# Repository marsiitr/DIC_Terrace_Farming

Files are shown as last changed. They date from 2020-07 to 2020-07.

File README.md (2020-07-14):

# DIC_Terrace_Farming
 Inter IIT Tech Meet 2019

<p align="center">
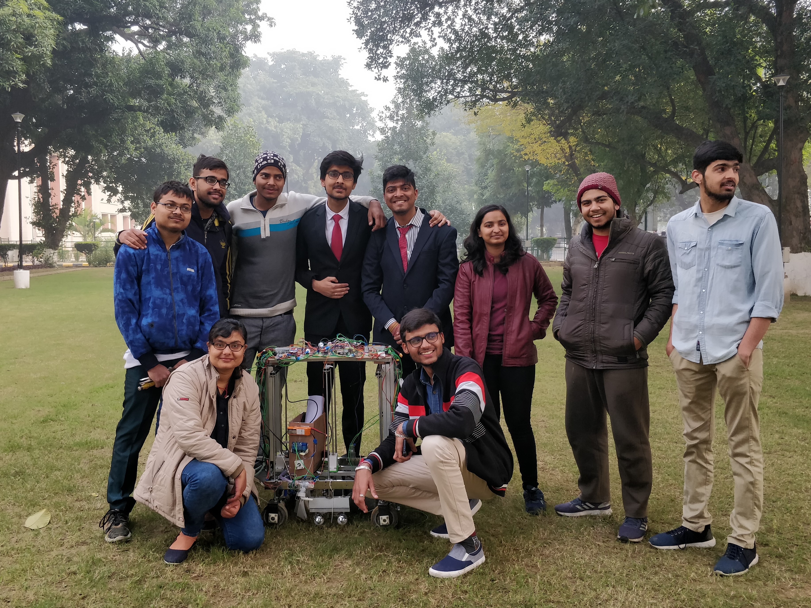
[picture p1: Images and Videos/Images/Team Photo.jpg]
  
  Team MaRS @Inter IIT Technical Meet 8.0
</p>

## Abstract:
<p align="justify">MaRS IIT Roorkee has developed an autonomous bot to perform agricultural tasks for terrace farming. This bot can perform functionalities like seeding, watering, ploughing and harvesting of the crops. It is itself unique in a way that the bot can climb up and down the manmade steps in the terrace farming.</p>

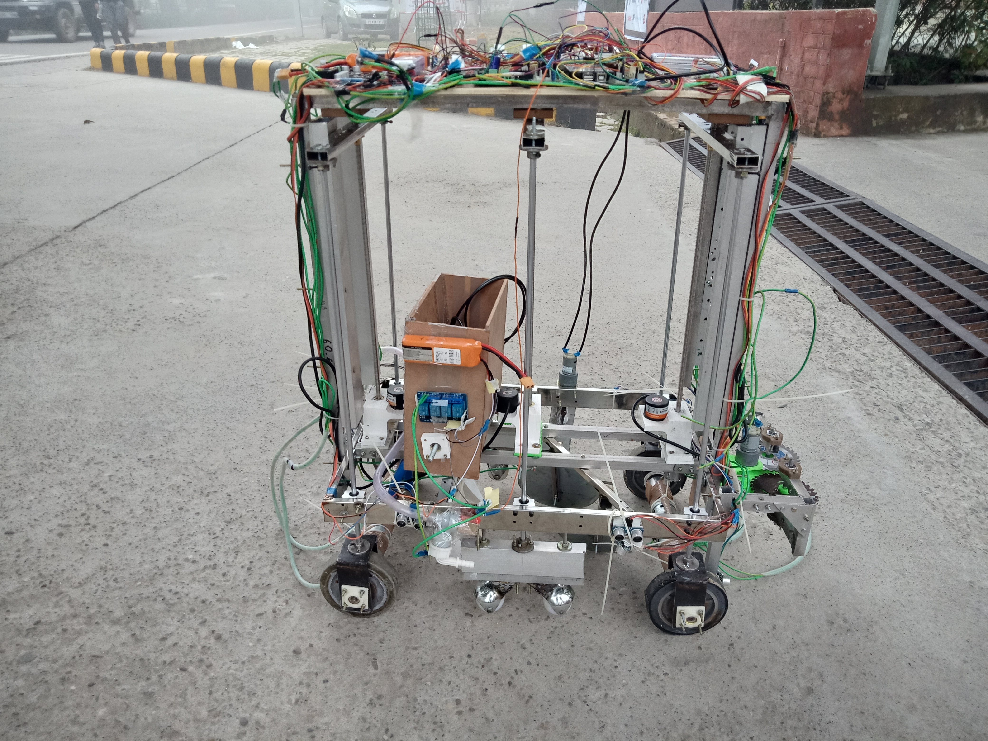
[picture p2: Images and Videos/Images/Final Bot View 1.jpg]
Terrace Farming Robot


To view more images of the final bot, click [here.](https://github.com/visvash/DIC_Terrace_Farming/tree/master/Images%20and%20Videos/Images "DIC_Terrace_Farming_Robot")

### Challenges faced in Terrace Farming:
* Narrow terraces make it difficult for the farmers to navigate. These also prevent the use of heavy machinery or animal power thus the farmers have to rely on locally made agricultural tools which are appropriate to narrow terraces. The use of improper tools and methods lead to poor yields.
* Improper irrigation methods and shortage of watering systems hamper the growth of the crops.
* Wider terraces demand the use of draft animals as a source of farm power. Sometimes farmers are compelled to use manual labour even for ploughing.
* Steeper slopes make it difficult for the farmers to mobilise the farming tools. It drastically increases the labour demand and hence increasing the cost of production.

## Mechanical Aspects of the Design

### Traversal
* The bot uses 4-wheel differential drive to traverse on the soil surface. Two central idler wheels are provided for extra stability while climbing the steps and traversing on uneven surfaces.
* For this drive we are using Mega Torque Planetary DC geared motor of 300RPM and torque capacity of 92kg-cm, enough to carry out tasks like Ploughing and Seeding. The chassis of bot is made up of square steel pipes, arc welded together for rigidity.

### Climbing
* We divided bot into 3-wheel assemblies in which front and back are containing 2 wheels, 2 motors and a lead screw but the middle assembly contains 4 caster wheels and a lead screw so that the bot does not topple, while one of the front or back wheel assemblies is in the air.
* In the first step, the whole body will be lifted by actuating the lead screws of middle and rear wheel assemblies. Then the bot will move forward until the front wheels rest above the step.
* In the second step, the Middle Caster Wheels will be pulled back up and the bot will move forward by actuating the back wheels to rest on the stair on front and middle wheels.
* In the last step, the back wheels will be pulled up, this time the front wheels will be actuating and it will move the bot forward and the bot would have climbed up.
* The bot also has an ability to lift itself above the crop for traversing in the field.

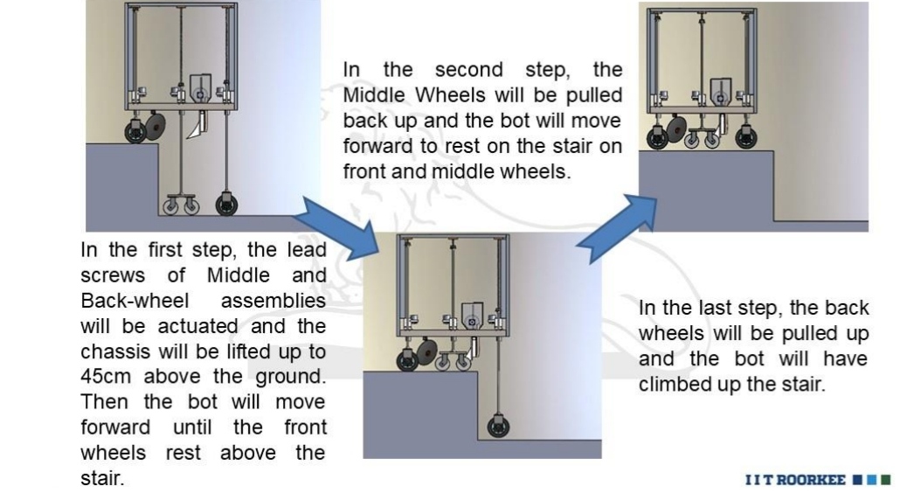
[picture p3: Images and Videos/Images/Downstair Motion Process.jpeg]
Climbing Process


### Ploughing
* The thickness of Topsoil for cultivation in terraces is less in comparison to that of plains and we can encounter stones while deep ploughing.
* Using a Disc Harrow mechanism for shallow ploughing would be more appropriate and will save the Tool from wear and tear. Simultaneously it will use less Power per unit area.
* A special concave disk having an angle of curvature of around 15-25 degrees has been used. This angle determines the ploughing depth. More the angle more is the depth of plough and more is the power to drive the operation.
* The discs also maintain an angle of 40-45 degrees with the direction of travel which helps it in rotation and opening of the soil by scooping it out simultaneously.

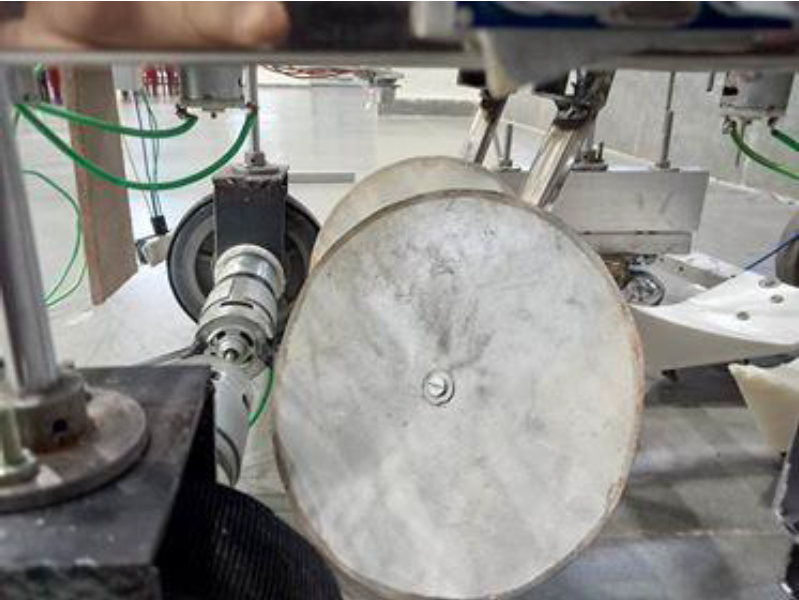
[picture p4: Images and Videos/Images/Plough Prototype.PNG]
Plough


### Watering
* The bot will have a solenoid-valve for electronically controlling the water given to the crops. 
* The concept of the watering mechanism is designed so as to minimize the water consumption along with maintaining the net yield.

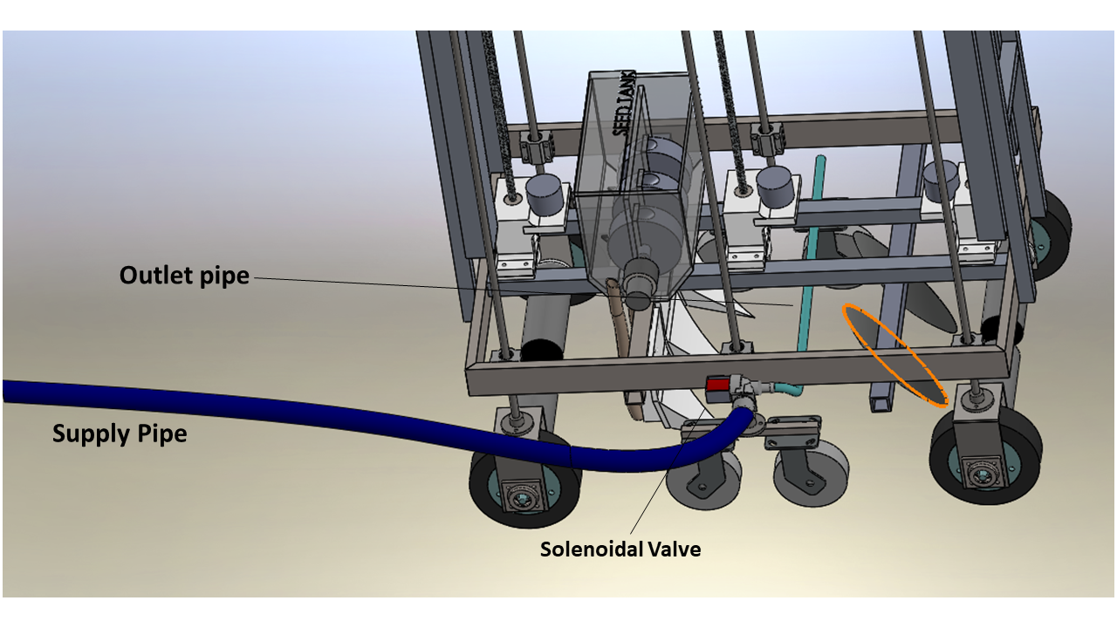
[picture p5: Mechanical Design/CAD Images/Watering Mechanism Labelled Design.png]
Watering Mechanism Design


### Seeding
* For dropping the seeds, a seed tank is attached on the bot that directs the seeds to the outlet pipes using 3D printed discs controlled by Johnson type DC motor. The tank contains 3 circular disc-like structures with grooves in them. These discs are rotated by the motor.
* The tank is divided into two-compartments, one compartment contains the seed and the other compartment contains the outlet. When the motor rotates the disc, the seeds are trapped in the grooves and are transferred to the next compartment. The seeds then fall to the ground through the outlet.
* Cultivator is mounted at the bottom along with outlet pipes at their back so they easily drop off seeds in the tillage so formed.

### Harvesting
• Harvester consists of 2 cutting blade, operated by a geared DC motor using Spur Gears.<br>
• Both the blades will rotate with the same speed but in opposite direction, the blades share a common
cutting area which will ensure cutting of crop which comes in between them.<br>
• The harvester can be detached and can be mounted on bot when required.

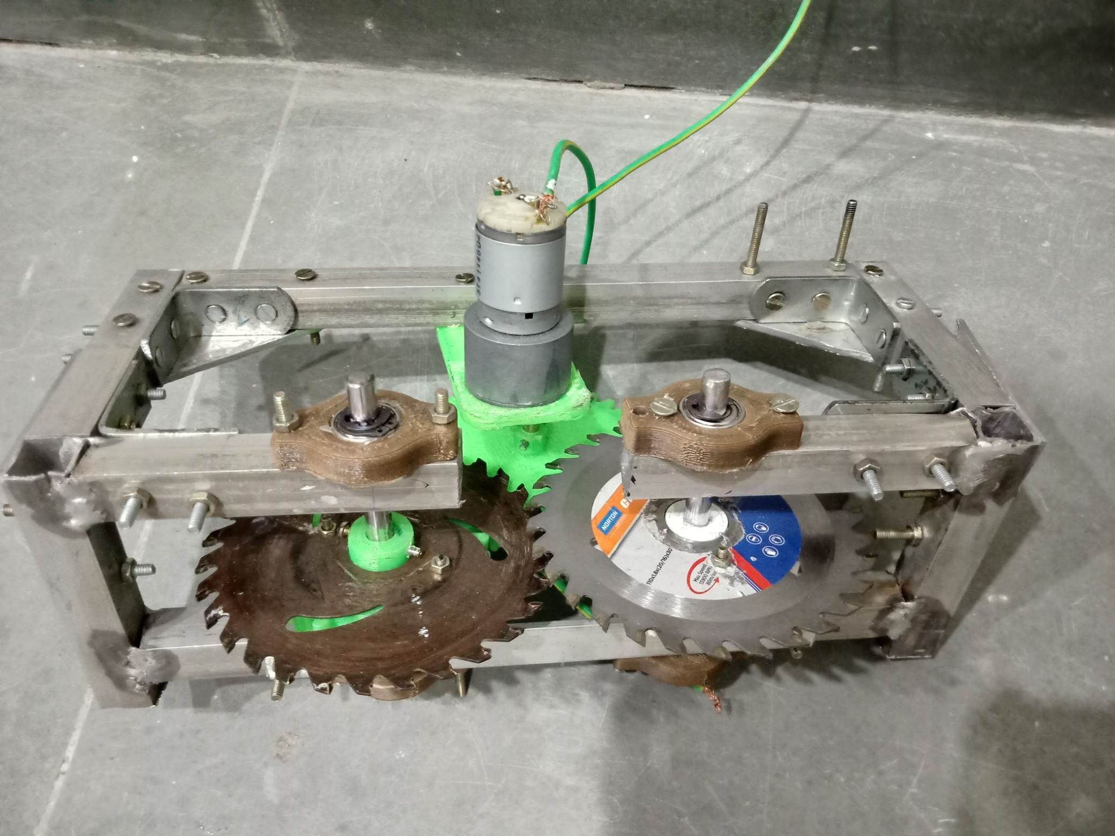
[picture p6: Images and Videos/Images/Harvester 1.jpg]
Harvester


## Electronic Aspects of the Bot
### Sensors Used:
#### ULTRASONIC SENSOR
8 such sensors are used.<br>

#### SOIL MOISTURE SENSOR
1 moisture sensor is used to take data inputs from the cultivated land.
#### TEMPERATURE SENSOR
1 temperature sensor is used to get the temperature data from the field.
#### ROTARY ENCODER 
3 rotary encoders is used to keep track of the lead screws during their operation. The DC motors used for the traversing of the bot has inbuilt encoders.
#### MPU 9250
1 such sensor is used. It contains gyroscope, accelerometer and magnetometer. It is used to maintain the orientation of the bot.
#### BUMP SENSOR
4 bump sensors are used to determine the state of the bot in certain manoeuvres.
#### HALL SENSOR 
Hall sensor is used to measure the distance travelled by the bot. Encoder cannot be used on the ground wheels as the wheel can slip on the ground which will result in wrong measurements.

### Micro-Controller:
<p align="justify">The microcontroller of the bot is the brain of the bot. Each and every function and maneuverer of the bot is controlled by a microcontroller. It also helps the bot take decisions and decides the further course of action. We have used Arduino Mega microcontroller board which depends on AT Mega microcontroller.
It includes digital input/output pins-54, where 16 pins are analogue inputs, 14 are used like PWM outputs hardware serial ports <b>(UARTs)</b> – 4, a crystal oscillator-16 MHz, an ICSP header, a power jack, a USB connection, as well as a RST button. This board mainly includes everything which is essential for supporting the microcontroller. So, the power supply of this board can be done by connecting it to a PC using a USB cable, or battery or an AC-DC adapter. This board can be protected from the unexpected electrical discharge by placing a base plate.</p>

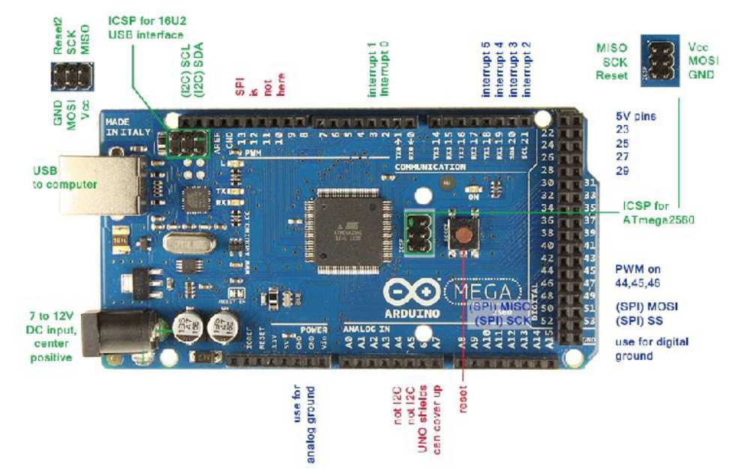
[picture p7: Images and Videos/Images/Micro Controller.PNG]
Sample Micro-Controller Image


### Motor Driver:
We have used the Cytron MDD10A which is a dual-channel version of the MDD10C. Like MD10C, MDD10A
also supports locked-antiphase and sign-magnitude PWM signal. 

### The Implication of PID:
PID is short for proportional, integral and derivative.
The PID is used to correct the error of the bot while traversing.

The correction value is given as<br>
**Correction = kp(error) + kd(error- previous_error)**

### Traversing:
* Traversing occurs with the help of ultrasonic sensors. Which is used to maintain a constant distance from the wall.
* After starting, the bot will stop successively after a fixed distance and take readings of various sensors and water the zone accordingly.
* Ploughing will occur automatically as the bot moves.<br>
* After detecting the end of the arena, the bot will take a 180 degree turn in the clockwise direction and move back to the respective starting zone.
* After detecting red or yellow region, bot will do the required action i.e. climbing up or down the steps.

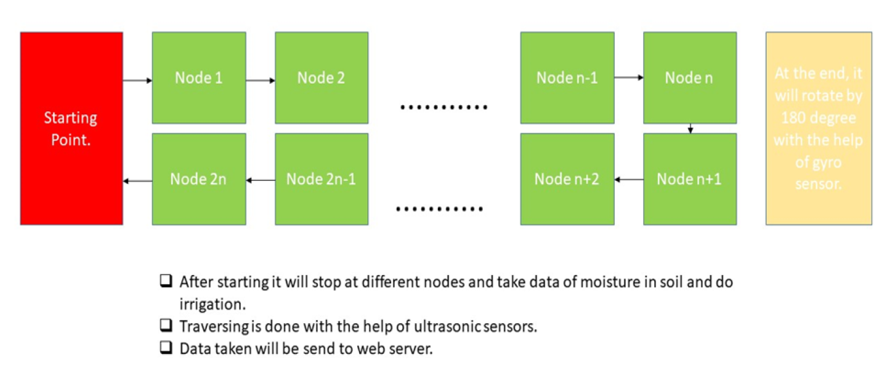
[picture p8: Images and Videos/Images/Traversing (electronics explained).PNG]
Traversing (Electronics Explained)


### Step Up Manoeuvre:
* For climbing mechanism, 3 lead screws are actuated using 3 DC motors, which lift the whole body in 3 steps.
* In the first step, the whole body will be lifted by actuating the lead screws of middle and rear wheel assemblies. Then the bot will move forward until the front wheels rest above the step. A bump sensor will detect that the front wheels have touched the ground. The front colour sensor will detect the change in the zone for the prior part of the bot (yellow to red).
* In the second step, the Middle Wheels will be pulled back up and the bot will move forward to rest on the stair on front and middle wheels.
* In the last step, the back wheels will be pulled up and the bot would have climbed up.
* The step-down manoeuvre is the opposite of the step up manoeuvre.
* The bot also has an ability to lift itself above the crop for traversing in the field.

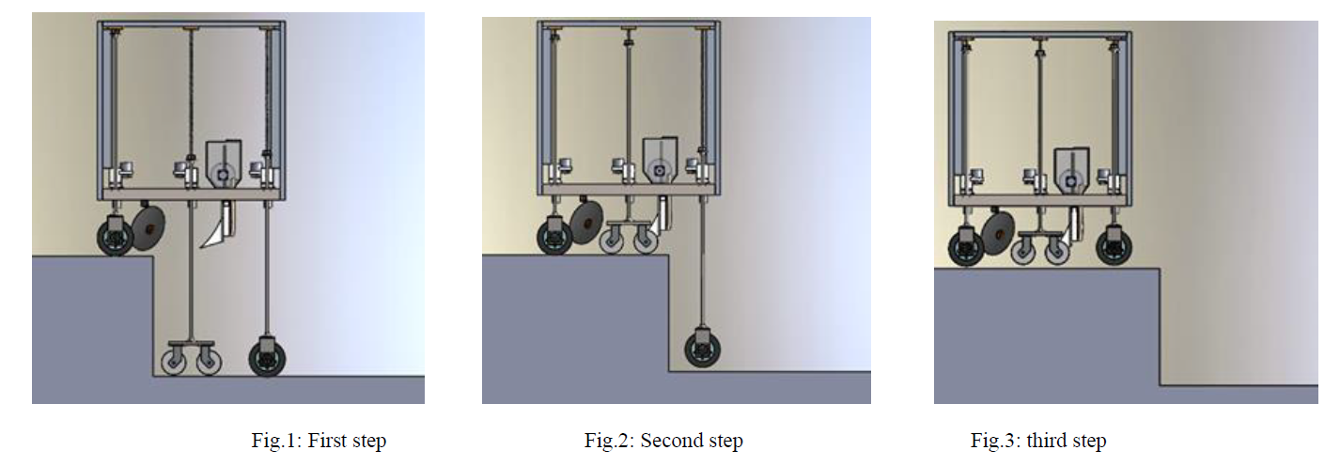
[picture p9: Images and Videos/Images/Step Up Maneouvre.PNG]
Step Up Manoeuvre


## Working of the IoT (Web Page)
<p align="justify">The readings from the different types of sensors (moisture, humidity, temperature etc) will be taken
by a microcontroller and transferred wirelessly to a database. The readings will be stored in the database
using file handling. The files with the reading will be sorted according to the nodes present on field.<br>
All the sensors are connected to the <b>Arduino AT Mega microcontroller</b>, which will be responsible for
registering the input data from the sensors. Since Arduino AT-Mega does not have a in-built Wi-Fi or
Bluetooth system, so a <b>ESP-8266 NODE-MCU</b> can be used to transfer the data wirelessly to the database.
The transfer of data from Arduino to the esp8266 can take place through interrupt pins, then the esp8266
will create a local server, another python script will run on a device having the database which will read the
data from the esp8266 and store it in a database using file handling. The micro-header named
<b>ESP_MICRO.h</b> is a very important header file needed for the esp8266 to transfer the data.<br>
After the data is stored in the database in a sorted manner, we will need to render the files to the web
page which will display the data to the user.</p> 

### Steps and Sequence of execution:
* Firstly, ensure proper connection of sensors with the Esp8266.
* Go to the folder named **IoT codes** present inside the **src** folder.
* Navigate inside to the **Esp8266 code** folder and Upload the file named **integrated.ino** in the Esp266.
* Upon running the code in Esp8266, it will generate an URL which needs to copied and pasted in the file named **PYTHON_READER.py**(generally the url remains same if the wifi connection of the Esp is not changed).
* Run the file named **PYTHON_READER.py** in the ubuntu terminal. (Upon execution, the data from sensors transmitted by Esp8266 will be read and written as a local text file)
* Finally run the **main.py** in the ubuntu terminal. It will generate an URL.
* Copy paste the URL in the browser to get to the web page.

*Note: The arrangement of the files inside the folder should be same as shown in the folder "IoT codes".<br><br>

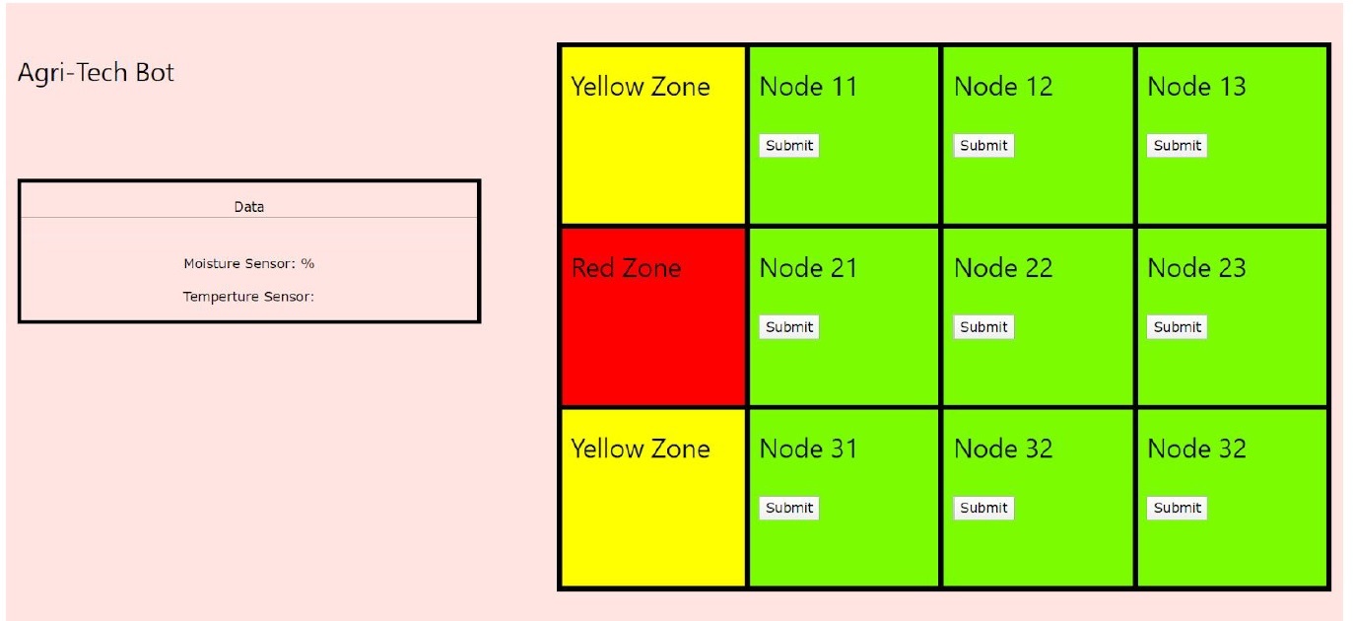
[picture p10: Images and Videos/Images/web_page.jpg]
Web Page


## Cost Structure:

 |Component       | Number used  | Cost INR|
 |---|----|---|
 | Planetary Geared Motor    |     4     |   19,996|
  |Arduino Mega 2560     |         1     |    800|
  |Node MCU Esp8266    |           1    |        260|
  |Motor Driver       |            6        |  15,000|
  |Battery            |           3      |  4997|
  |Heavy Duty Wheels   |             4          |    900|
  |Caster Wheels        |           4     |   200|
  |Johnson motor             |  5     |        1996|
  |Rotary Encoder     |             3   |        4497|
  |Ultrasonic Sensor  |             5    |         900|
  |Mpu9250           |             1    |          190|
  |Dht11 temperature  |              1     |     108|
  |Soil Moisture Sensor  |            1    |        75|
  |Bump Sensor           |           4     |        400|
  |Lead screw            |         3       |    2397|
  |Material for Body    |          ----   |        4000|
  |Manufacturing            |      ----  |         3500|
|<b>Total Cost- </b>   |     |   **60,216**|

## Future Improvement
### • Weed Detection:
Weed Removal Technology can be a boon for
the farmers because weeds reduce the yield and
quality of crops by competing for nutrients,
water and sunlight. Weeds intensify the pest and
disease problem by serving as alternate host.<br>

They also reduce the efficiency of harvesting
and hence resulting in land value reduction.

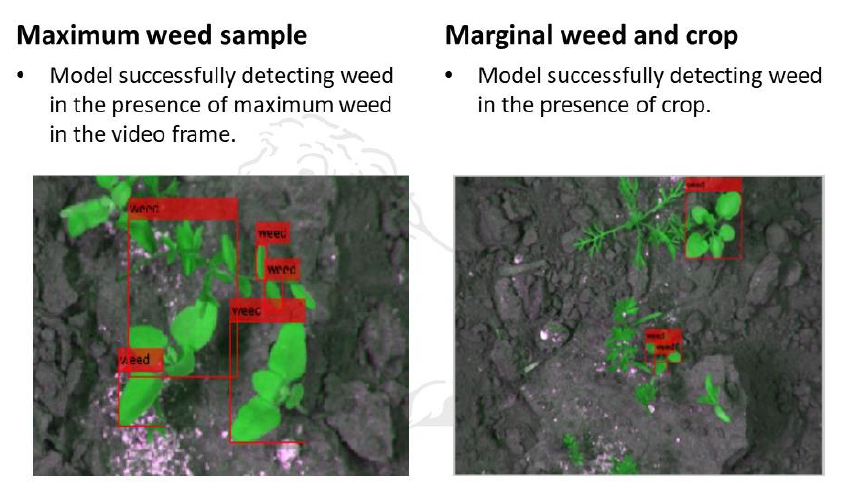
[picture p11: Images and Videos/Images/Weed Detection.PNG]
Weed Detection Image


A **high-resolution camera** is mounted on the bot to capture live feed video. The detection tool uses
machine learning procedure based on support vector machines and blob analysis for effective
classification of weed.<br>
Training of the model is done based on 3 scenarios:<br>
1. Maximum crop sample.
2. Maximum weed sample.
3. Marginal weed and crop sample.

The trained module is expected to achieve a success percentage of 59-95% to detect the weed.

### • Solar Powered:
<p align="justify">We are also planning to use the solar power supply to meet all the power demands, so that this bot
becomes accessible to even those regions of the country where electric supply is scarce. This Agritech
bot operates on 12V Li-ion battery which can be charged using solar power.</p>

#### Team Members
1. [Annushree](https://github.com/annushree21)<br>
2. [Avdesh Kumar Ranwa](https://www.linkedin.com/in/avdesh-kumar-ranwa-a43610187/)<br>
3. [Debaditya Barman](https://github.com/ItZ-Debaditya)<br>
4. [Dhruv Shehgal]( https://github.com/Dhruv1064)<br>
5. [Naveen Chandra Rai](https://github.com/ncr38)<br>
6. [Ruchika Guntewar](https://github.com/RuchikaGuntewar)<br>
7. [Shashi Muchkund](https://github.com/smuchkund)<br>
8. [Shubham Goyal](https://github.com/shubham491981)<br>
9. [Tabish Madni](https://github.com/Tmadni)<br>
10. [Visvash Attri](https://github.com/visvash)<br>

#### Mentors
1. [Anant Shandilya](https://www.github.com/Anant-Shandilya)<br>
2. [Shubhanshu Agarwal](https://github.com/Shubhanshu07)

<p align="center">
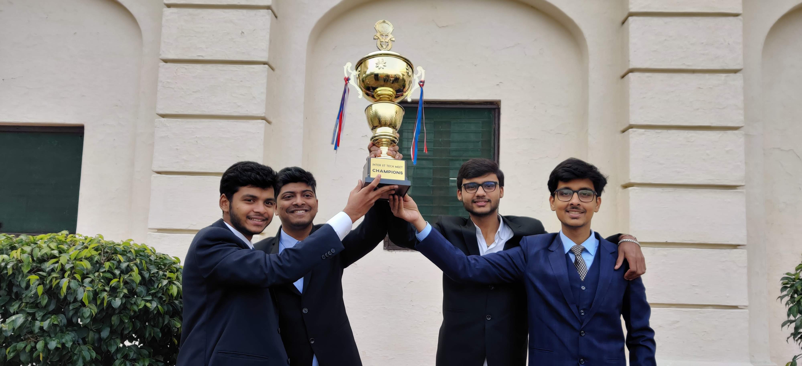
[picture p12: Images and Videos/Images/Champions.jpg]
  
  Inter IIT Tech-Meet Champions
</p>

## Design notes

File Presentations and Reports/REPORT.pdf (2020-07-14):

# DIC’s Terrace Farming Robot

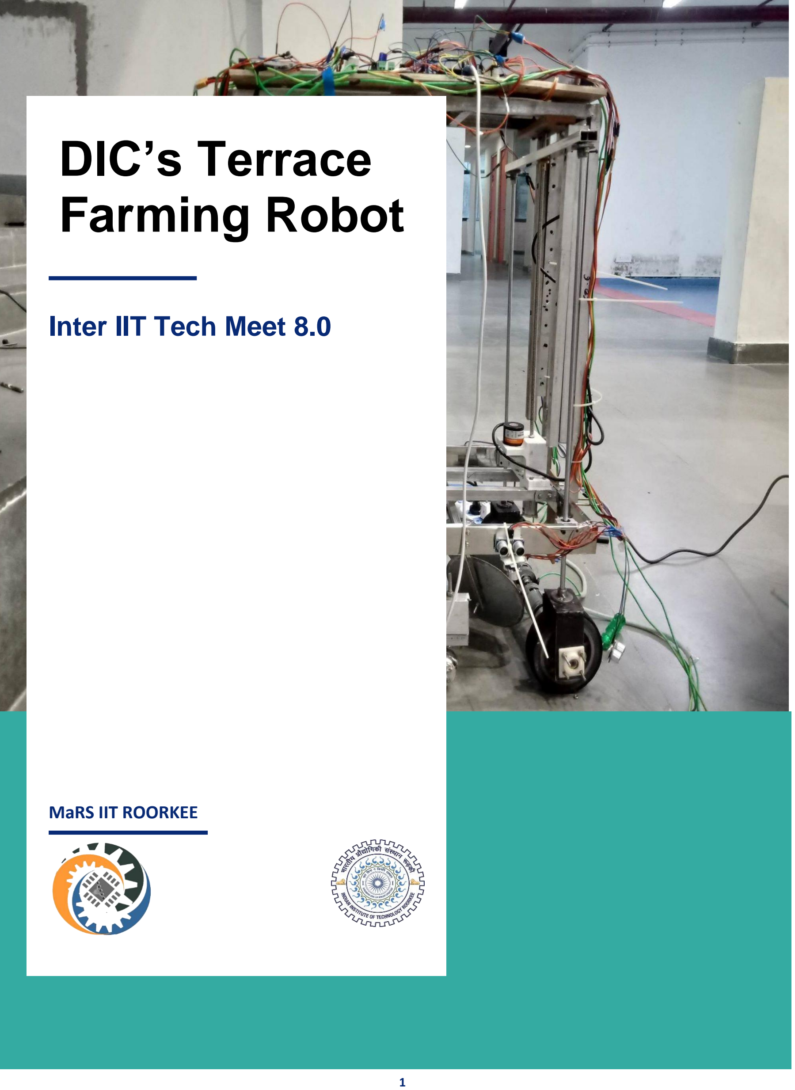
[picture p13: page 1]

1

# Inter IIT Tech Meet 8.0

### MaRS IIT ROORKEE

2

# Team Members

## Annushree

## Avdesh Kumar Ranwa

## Debaditya Barman

## Dhruv Shehgal

## Shashi Muchkund

## Shubham Goyal

## Visvash Attri

3

## Contents

- Overview - Project Motivation - Products available in the market - Field visit- Village Bhatta Gaon - Survey with Local Stakeholders - Market - Our Solution of the Agritech Bot a. Features b. Innovation - Mechanical Aspects of the Agritech Bot a. Traversal b. Climbing c. Ploughing d. Watering e. Seeding f. Harvesting - Electronic Aspects of the Agritech Bot a. Sensors Used b. Microcontrollers c. Implication of PID d. Working of IoT (Web Page) e. Using Flask - Solving the Problem Statement - Cost Structure - Proposal of Real Life Solution

4

## Overview

MaRS IIT Roorkee has developed an autonomous bot to perform agricultural tasks for terrace farming. This bot can perform functionalities like seeding, watering, ploughing and harvesting of the crops. It is itself unique in a way that the bot can climb up and down the manmade steps in the terrace farming.

## Project Motivation

The UN Food and Agriculture Organization predicts that we need to boost worldwide food production by 70 percent over the next several decades in order to feed the anticipated population of 2050. Many regions in India are hilly with sparse crop production, which with proper planning can be graded to better agricultural spots.

Terrace farming is widely practiced in India in the states of Meghalaya, Uttarakhand, Himachal Pradesh and Haryana. Among the 34 million people inhabitant in the Himalayan region, a large percentage of the population are dependent on hill farming. 15.8 percent of the total area of Himalayas i.e. 53.8 million Hectares are farmlands and 37 percent are sloping lands of various degrees. Being an integral part of the farming culture in India, the farmers are predominantly facing challenges in practicing the same. This project aims to provide a technical, cost-effective and reliable solution to the challenges faced by the farmers while practicing terrace farming.

The challenges faced in terrace farming are:

1) Narrow terraces make it difficult for the farmers to navigate. These also prevent the use of heavy machinery or animal power thus the farmers have to rely on locally made agricultural tools which are appropriate to narrow terraces. The use of improper tools and methods lead to poor yields.
2) Improper irrigation methods and shortage of watering systems hamper the growth of the crops.
3) Wider terraces demand the use of draft animals as a source of farm power. Sometimes farmers are compelled to use manual labour even for ploughing.
4) Steeper slopes make it difficult for the farmers to mobilise the farming tools. It drastically increases the labour demand and hence increasing the cost of production.

## Products available in the market

The relevant existing solution which pertains to the autonomous implementation of the basic agricultural functionalities are:

1. Naio Technologies: Can automate weed detection, assist during hoe and harvesting.
2. Energid Citrus picking system: Automates harvesting of citrus fruits.
3. Blue River LettuceBot 2: Assists the farmer in cultivating lettuce crops. Has an inbuilt imaging system which helps in weed-detections.
4. Vision Robotics: Automates the process of seeding and harvesting.

None of the above machines is available in India. Neither any of the solution mentioned has the ability to climb the steps of the field cultivated by terrace farming. The existing solutions are customized to perform only limited tasks. Using a bot for a specific purpose will increase the cost of farming and is thus no economical. The solutions mentioned generally have very high cost of purchase and maintenance.

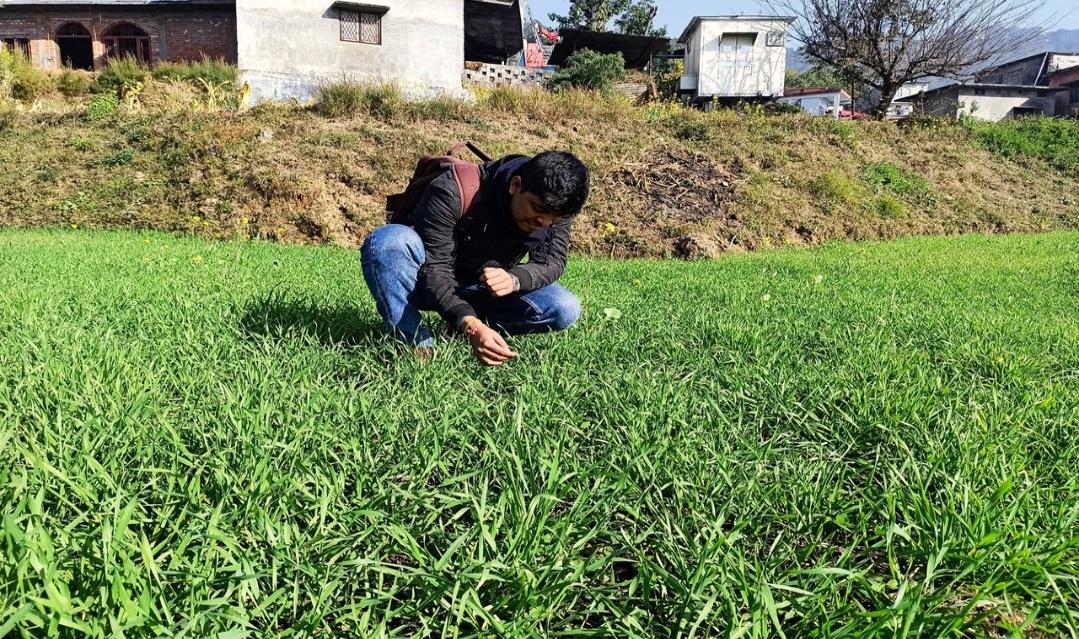
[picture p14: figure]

5

## Field Visit - Village Bhatta Gaon

A survey and a field visit were conducted by our team in order to find the real challenges that the farmers face while practicing terrace farming. The field visit helped in getting a real live analysis of the dimensions of the terrace field, quality and moisture content of the soil.
The place of survey was Bhatta Gaon (30.4348° N, 78.0780° E). It is a small village in Uttarakhand located at an altitude of about 8000 meters above the sea level, about 94 kms from IIT Roorkee. The place for the study was decided by analyzing the terrain regions from Google maps. Our aim was to find the closest place from Roorkee where terrace farming is a mainstream occupation of the people and has a fair amount of connectivity.

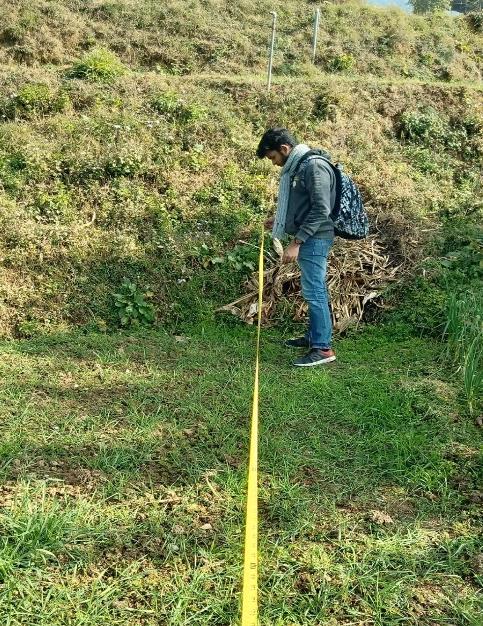
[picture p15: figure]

## Survey/Talking with Local Stakeholders

The family of Ram Jadwan depends on the terrace farming to fill their stomachs. He and his wife Mira Jadwan jointly run their ventures on their farm. We had the opportunity to ask a few questions to them.

Here is a conversation between Ram Jadwan (Local Farmer), Mira (his wife) and Debaditya (Team MaRS):

Debaditya: What is the actual problem faced by the farmers here?

Ram: Lands are dispersed, no roads to navigate, No equipment available, No irrigation.

Debaditya: What crops are mainly grown on the land?

Ram: Wheat, makki and jawar.

Debaditya: How do you navigate through steps?

Ram: Small kachcha road craven out though the steps.

Debaditya: What modern equipment are used by them to assist in their farming? Do you use tractors?

Ram: No modern equipment only hand driven tools.

Debaditya: What are the government schemes that tends to assist the farmers?

Ram: No government schemes. No help from them.

Debaditya: Is the yield of the products less? If yes then why? And how can it be increased?

Ram: Yes, it is very less. Land dispersion should be decreased. Poor quality seeds and no irrigation facility.

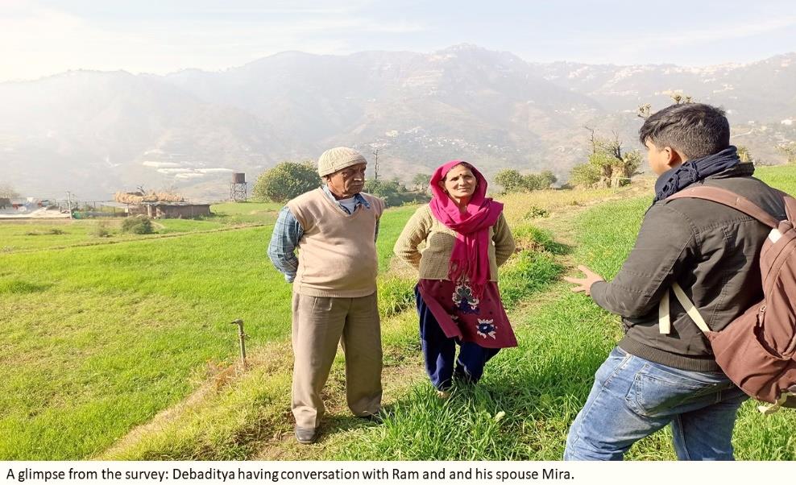
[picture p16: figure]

6

Debaditya: Will they be interested in the use of robot which can help them is terrace farming?

Ram: Yes, they will explore if the product yield increases.

Debaditya: Do you think technology can increase yield?

Ram: Yes, technology can increase yield.

Debaditya: Do you have a smartphone?

Ram: Not really but their son has one.

Debaditya: Are people migrating from
mountains to cities? If yes then Why?

Debaditya: No money in farming. No money to feed the family for one month.

Ram: Yes.

Debaditya: What about water supply?

Ram: No water for irrigation.

Debaditya: How much land do you own? And what is the profit?

Ram: 8-10 Bigha. Very less profit. Mostly crops grown for family needs.

Debaditya: Is their home accessible by road?

Ram: No.

Debaditya: Seeds used?

Ram: 10-12 kg for 8-10 bigha land.

Due to the time constraints, the survey could be completed with only 21 such families. Most of the families were having at least one smartphone in their family. A large section of them own less than 10 bigha land out of which most of it remains uncultivated. Some population of the farmers believe that the government should provide them with such technological solutions.

## Land Owned By Locals

1-5 Bigha

6-10 Bigha

10-15 Bigha
15 Bigha or More | Yes
No

Can't
Say

## CURIOUS FOR A ROBOTIC SOLUTION

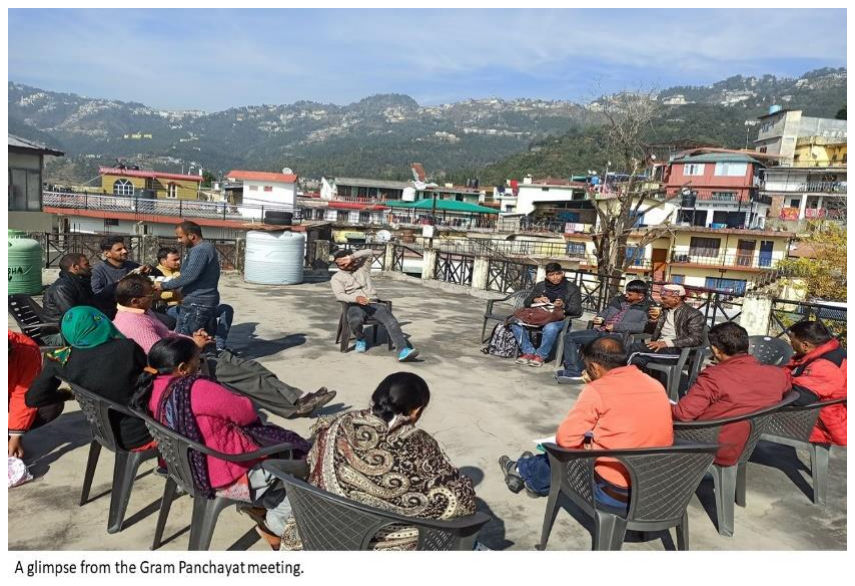
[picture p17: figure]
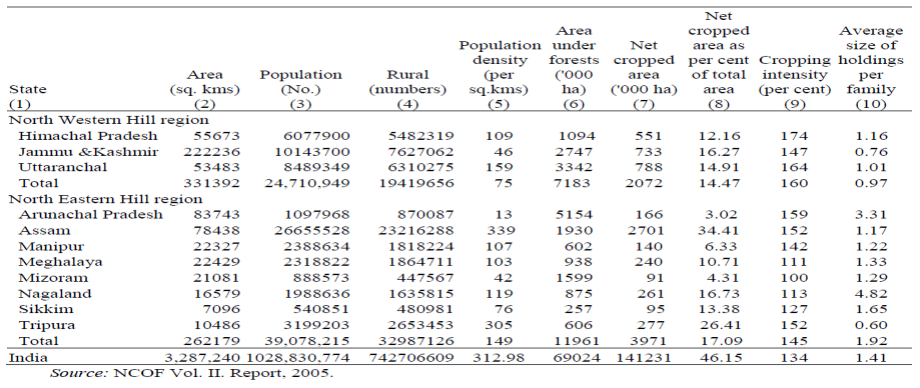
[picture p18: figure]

7

Attending the Gram Panchayat
Team Members also attended the Gram Panchayat and came across the various viewpoints of the people regarding terrace farming. Village Pradhan personally met the team and discussed about the problems of manual labor and less efficiency of yield. He also remarked about the role of the government and said that the government and the engineers of the country should come forward for providing these farmers with proper technology.

## Market

According to a survey conducted by NCOF, among the 34 million people that inhabit the Himalayan region 80 percent of the people are dependent on hill farming. 48 percent among them practice farming on sloping lands i.e. terrace farming.

Going by the statistics shown in the table, the population dependent on hill farming in India will account to about 823,064,619.2 and the population practising on sloping lands will amount to about 395,071,071.216.
Our solution targets the farmers who are practicing farming on sloping lands and identifies them as the primary user of the product. The method of deployment of the product can be different in different scenarios. The product can be deployed by the government as an aid to the farmers. In this case the government will be the customer. The product can be acquired by an individual farmer which makes him/her as the customer.

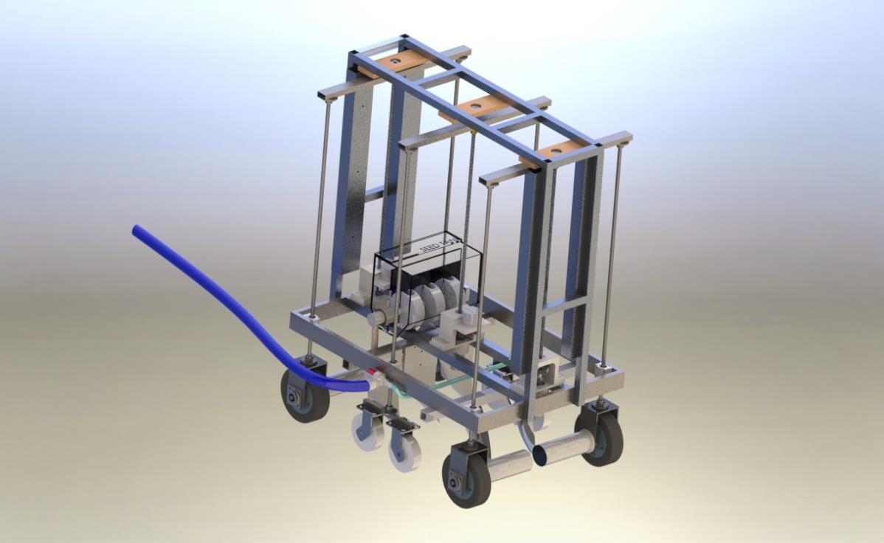
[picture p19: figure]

8

## Our Solution

9

## Features:

1. Basic agricultural functionalities: The bot can perform the basic agricultural functions for the farmers. The basic functions include.
a. Ploughing
b. Watering
c. Seeding
d. Harvesting
2. Sensors: Installed with advanced sensors like moisture, humidity, temperature etc. to get the data inputs.
3. IOT enabled: Display sensor data on a web page. The bot can be controlled as per user discretion.
4. Alert System: A centralized alert system governs the bot. It can alert the user in case of:
1. Shortage of Seeds
2. Low power
3. Internal damage
5. Solar powered: The bot can be customized to run on solar powered panels.

## Innovation

- IOT enabled: In the present age, farming in the western countries are heavily influenced by the modern technologies. They have adopted the principle of smart farming. Sensors are frequently used by them to check the soil and weather conditions and this helps them in taking important decisions. However, the farmers of India are way behind in this aspect.
Our aim is to take the farmers in the loop. Making a bot which only completes the basic agriculture functions without any human interruptions will lead to ignorance of farmers towards the technologies. This particularly defeats the purpose of making the farmers smart. Also, the farmers lack inputs from their lands, Therefore the idea of implicating IOT in our bot is an important step taken towards making the farmers smart.
Our bot is integrated with IOT. Three particular sensors are used to determine the soil moisture content, humidity and temperature. The detailed working of the IOT is discussed in later sections. The inputs from these sensors can help the farmer in determining: -
- The region where irrigation is needed.
- Amount of water needed for irrigation.
- The temperature gradient in the farmland (generally terrace farm of each ranges to about 600m hence a difference in temperature gradient)
Our bot is automated to water the fields according to the sensor readings. This functionality can be customized by the farmers according to their need.
- Height Adjustable Chassis: The chassis of the bot is supported by three lead screws which in turn is driven by three motors. This unique design of the bot helps to uplift the entire chassis of the bot to the height desired to perform a particular task. For e.g. while watering the crops the chassis can be lifted above the height of crop, this ensures that the crops are not hampered by the motion of the Agri tech bot as it moves forward. 4 start lead screw nuts have been used because they multiply the total effective power developed by a large factor.

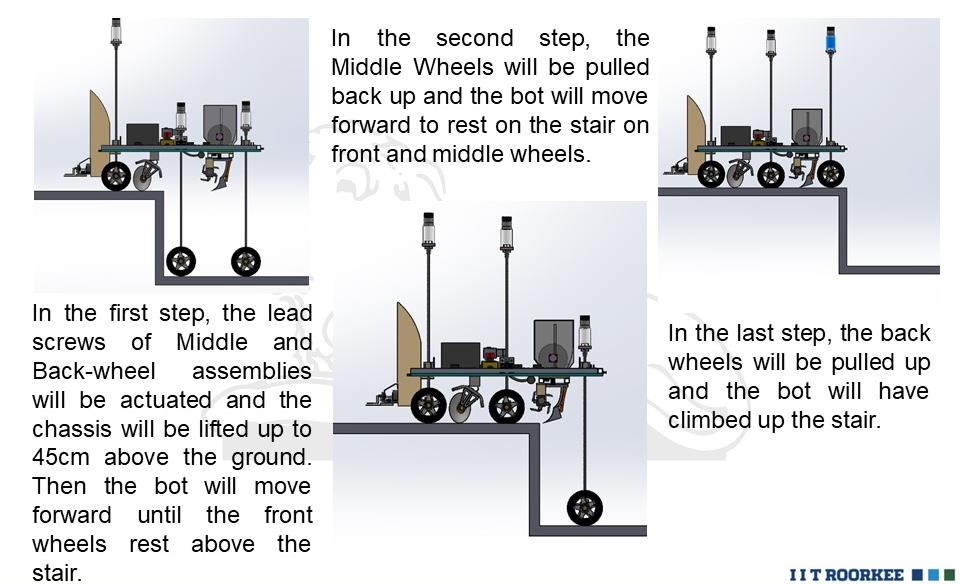
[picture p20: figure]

10

Mechanical Aspect of the bot.

Traversal

- The bot uses 4-wheel differential drive to traverse on the soil surface. Two central idler wheels are provided for extra stability while climbing the steps and traversing on uneven surfaces.
- For this drive we are using Mega Torque Planetary DC geared motor of 300RPM and torque capacity of 92kg-cm, enough to carry out tasks like Ploughing and Seeding.
- The chassis of bot is made up of square steel pipes, arc welded together for rigidity.

Climbing

- We divided bot into 3-wheel assemblies in which front and back are containing 2 wheels, 2 motors and a lead screw but the middle assembly contains 4 caster wheels and a lead screw so that the bot does not topple, while one of the front or back wheel assemblies is in the air.
- In the first step, the whole body will be lifted by actuating the lead screws of middle and rear wheel assemblies. Then the bot will move forward until the front wheels rest above the step.
- In the second step, the Middle Caster Wheels will be pulled back up and the bot will move forward by actuating the back wheels to rest on the stair on front and middle wheels.
- In the last step, the back wheels will be pulled up, this time the front wheels will be actuating and it will move the bot forward and the bot would have climbed up.
- The bot also has an ability to lift itself above the crop for traversing in the field.

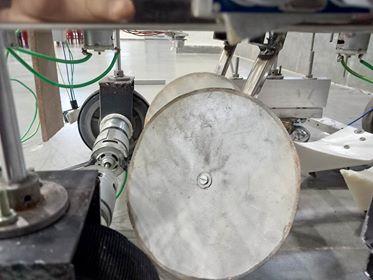
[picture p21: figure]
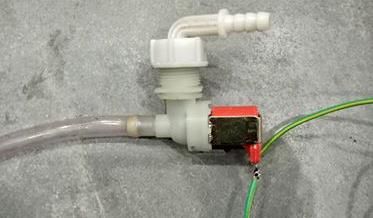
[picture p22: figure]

11

Ploughing

- After reading about different Ploughing mechanisms we used Disc Harrow mechanism instead of disc Plough. Because when we visited fields of “Bhatta Gaon”, we found out that the thickness of Topsoil for cultivation is less in comparison to that of plains and we can encounter stones while deep ploughing.
- Using a Disc Harrow mechanism for
shallow ploughing would be more
appropriate and will save the Tool from wear and tear. Simultaneously it will use less Power per unit area.
- A special concave disk having an angle of curvature of around 15-25 degrees has been used. This angle determines the ploughing depth. More the angle more is the depth of plough and more is the power to drive the operation.
- The discs also maintain an angle of 40-45 degrees with the direction of travel which helps it in rotation and opening of the soil by scooping it out simultaneously.

Watering

- Keeping in mind that a reservoir has already been provided, we are using a pipe with a pump that will water the crops using the sprinkle irrigation method close to the roots of the crops.
- The bot will have a solenoid-valve for electronically controlling the water given to the crops. The concept of the watering mechanism is designed so as to minimize the water consumption along with maintaining the net yield.

12V Solenoidal Valve

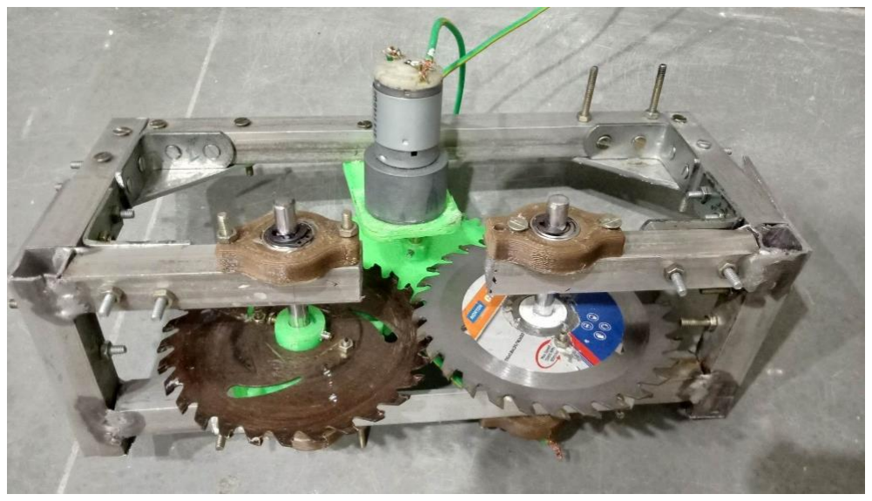
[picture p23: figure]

12

Seeding

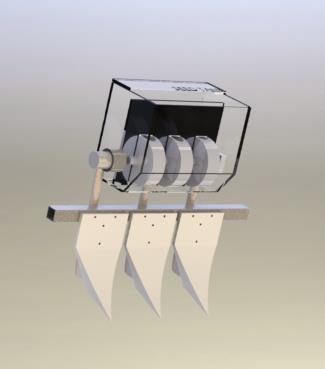
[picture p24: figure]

- For dropping the seeds, a seed tank is attached on the bot that directs the seeds to the outlet pipes using 3D printed discs controlled by Johnson type DC motor. The tank contains 3 circular disc-like structures with grooves in them. These discs are rotated by the motor.
- The tank is divided into two-compartments, one compartment contains the seed and the other compartment contains the outlet. When the motor rotates the disc, the seeds are trapped in the grooves and are transferred to the next compartment. The seeds then fall to the ground through the outlet.
- Cultivator is mounted at the bottom along with outlet pipes at their back so they easily drop off seeds in the tillage so formed.

Harvesting

- Harvester consists of 2 cutting blade, operated by a geared DC motor using Spur Gears.
- Both the blades will rotate with the same speed but in opposite direction, the blades share a common cutting area which will ensure cutting of crop which comes in between them.
- The harvester can be detached and can be mounted on bot when required.

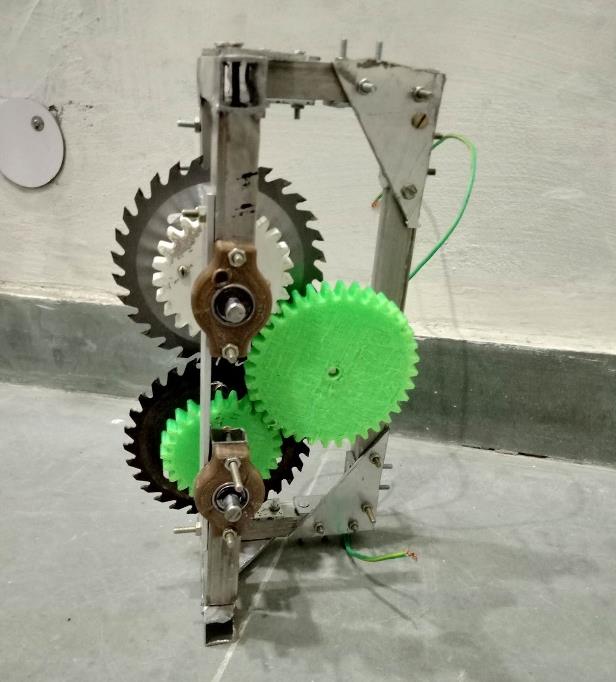
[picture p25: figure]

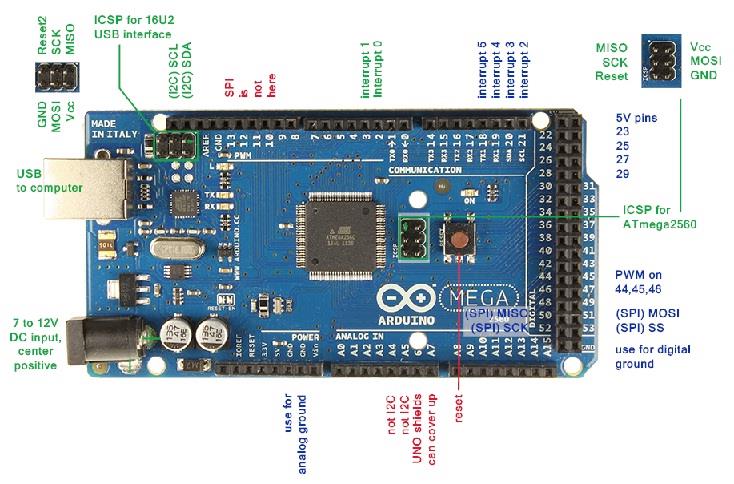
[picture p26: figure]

13

## Electronics aspect of the bot

Sensors Used

1. ULTRASONIC SENSOR: 5 such sensors are used. Mainly used to maintain constant distance from wall while traversing.
2. SOIL MOISTURE SENSOR: 1 moisture sensor is used to take data inputs from the cultivated land.
3. TEMPERATURE SENSOR: 1 temperature sensor is used
to get the temperature data from the field.
4. ROTARY ENCODER: 3 rotary encoders is used to keep

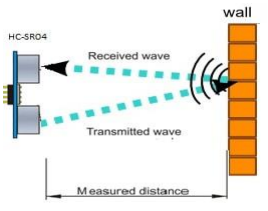
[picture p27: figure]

track of the lead screws during their operation. The DC motors used for the traversing of the bot has inbuilt encoders.

5. MPU 9250: 1 such sensor is used. It contains gyroscope, accelerometer and magnetometer. It is used to maintain the orientation of the bot.
6. BUMP SENSOR: 4 bump sensors are used to determine the state of the bot in certain manoeuvres.
7. HALL SENSOR: Hall sensor is used to measure the distance travelled by the bot. Encoder cannot be used on the ground wheels as the wheel can slip on the ground which will result in wrong measurements.

## Micro-Controller

The microcontroller of the bot is the brain of the bot. Each and every function and maneuverer of the bot is controlled by a microcontroller. It also helps the bot take decisions and decides the further course of
action. We have used Arduino Mega microcontroller board which depends on AT Mega microcontroller.

It includes digital input/output pins-54, where 16 pins are analogue inputs, 14 are used like PWM outputs hardware serial ports (UARTs) (https://www.elprocus.com/basics-of-uart-communication-block-diagram-applications/) – 4, a crystal oscillator-16 (https://www.elprocus.com/crystal-oscillator-circuit-and-working/) MHz, an ICSP header, a power jack, a USB connection, as well as a RST button. This board mainly includes everything which is essential for supporting the microcontroller. So, the power supply of this board can be done by connecting it to a PC using a USB cable, or battery or an AC-DC adapter. This board can be protected from the unexpected electrical discharge by placing a base plate.

Fig Arduino AT MEGA

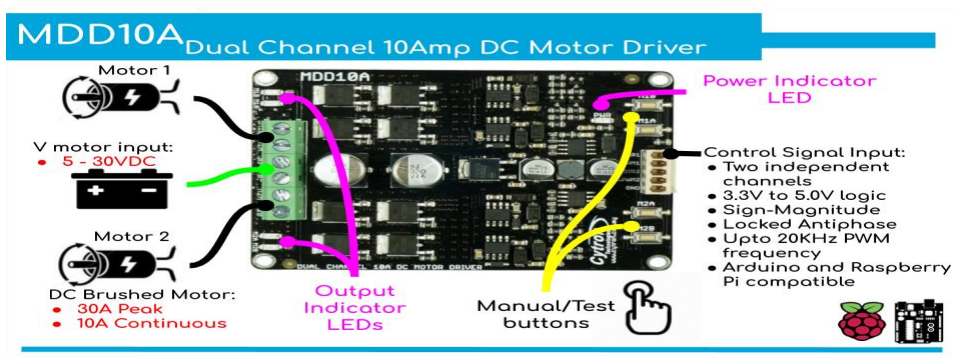
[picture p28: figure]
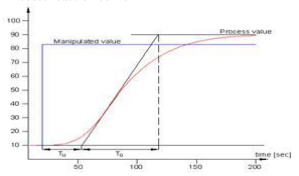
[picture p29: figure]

14

## Motor Driver

The DC motors used in the bot are being controlled by the microcontroller through a motor driver. A motor driver enables the Arduino to control over the speed, direction and PWM of the motors.

We have used the Cytron MDD10A which is a dual-channel version of the MDD10C. Like MD10C, MDD10A also supports locked-antiphase and sign-magnitude PWM signal. It uses full solid-state components that offers faster response time and eliminates the wear and tear of the mechanical relay. It can support V-motor from 5V to 30VDC. With the pre soldered terminals, and on-board manual/test buttons, you can get started even without any microcontroller.

## The Implication of PID

PID is short for proportional, integral and derivative. The name comes from the methods on how such controller deals with disturbances in the system. However, such a controller is only in feedback systems. The PID is used to correct the error of the bot while traversing.

Trial and Error Method: It is a simple method of PID controller tuning. While the system or controller is working, we can tune the controller. In this method, first, we have to set Ki and Kd values to zero and increase the proportional term (Kp) until the system reaches to oscillating behaviour. Once it is oscillating, adjust Ki (Integral term) so that oscillations stop and finally adjust D to get a fast response.

Process reaction curve technique: It is an open-loop tuning technique. It produces a response when a step input is applied to the system. Initially, we have to apply some control output to the system manually and have to record the response curve.After that, we need to calculate slope, dead time, the rise time of the curve and finally substitute these values in P, I and D equations to get the gain values of PID terms.

Process reaction curve

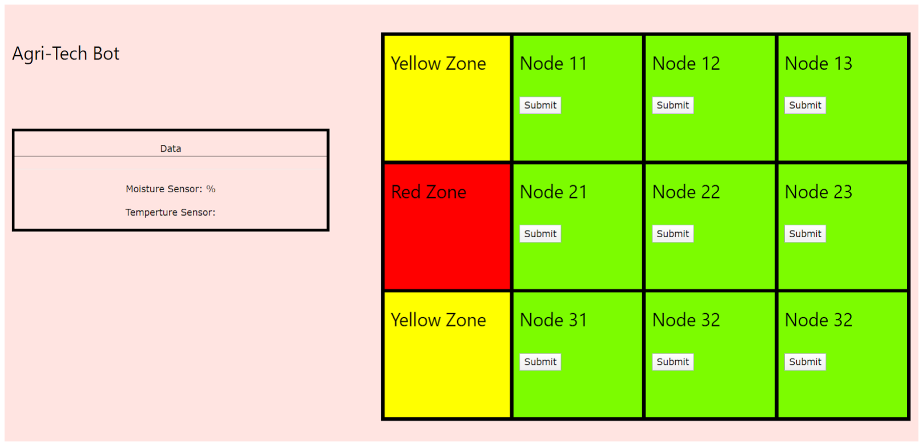
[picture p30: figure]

15

## Working of the IOT (Web Page)

One of the problems faced by the farmers in terrace farming is the lack of data from the land but this feature of the Agritech bot is the solution to the problem faced. The Agritech robot is envisioned to make the farmers smart, robust and decrease the human dependency.
The readings from the different types of sensors (moisture, humidity, temperature etc) will be taken by a microcontroller and transferred wirelessly to a database. The readings will be stored in the database using file handling. The files with the reading will be sorted according to the nodes present on field. A node is a region/area on the actual cultivated land whose details can be obtained in order to analyse the condition of the soil and the crops.

All the sensors are connected to the Arduino AT Mega microcontroller, which will be responsible for registering the input data from the sensors. Since Arduino AT-Mega does not have a in-built Wi-Fi or Bluetooth system, so a ESP-8266 NODE-MCU can be used to transfer the data wirelessly to the database. The transfer of data from Arduino to the esp8266 can take place through interrupt pins, then the esp8266 will create a local server, another python script will run on a device having the database which will read the data from the esp8266 and store it in a database using file handling. The micro-header named
ESP_MICRO.h is a very important header file needed for the esp8266 to transfer the data.
After the data is stored in the database in a sorted manner, we will need to render the files to the web page which will display the data to the user. The web page is thus an essential entity here. The web page contains a responsive replica of the land under cultivation. A basic snapshot of the web page looks like the picture as shown below.

The Web page Interface

16

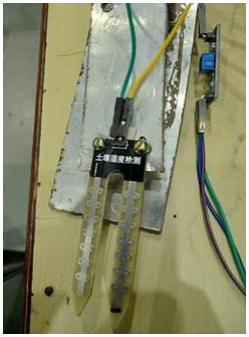
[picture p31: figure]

The table on the right-hand side is the replica of the cultivated land and in our case is the arena for the problem statement. The table is responsive and will respond to the click of the user. Each step is divided into different nodes. It is the region where the Agritech bot will take the readings from the sensors.
The user has to click on the submit button on the nodes whose conditions/readings he wants to analyse. The details of the sensor reading will be displayed on the box present on the right-hand side of the web page. The data from the database will be rendered to the website using flask. A note/message can be delivered regarding what can be expected of the readings.

A simplified flow-chart of the process:

## Sample Esp8266 code

This sample code will run on esp8266. The code creates a local server and hosts the sensor data to the same local server. Another python script which connects to the same local server will be able to read the data hosted on the local server and simultaneously create a text file for each node with data for the respective node.

Soil moisture sensor

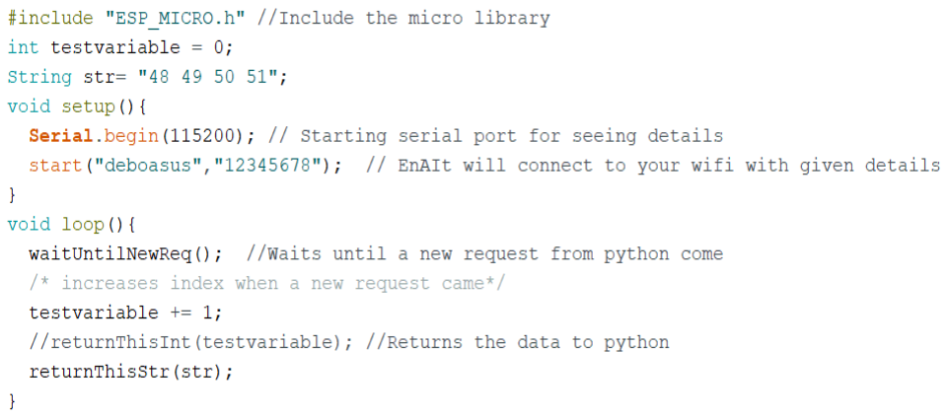
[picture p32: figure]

17

## Python Script on receiving end

The sensor data sent by the Esp8266 to the local host needs to transferred to a database. In our case we have used laptop as a database for the storage of the sensor data. The process of reading the data from the local host and writing it to a database is done by a python script that runs on the same computer where the database is located. The snippets of the code are explained below.

import urllib.request (This is the library that needs to be imported. This library enables the code to link to the url as defined in the next line.

url = "http://192.168.137.161/" # ESP's url, (Esp serial prints it when connected to wifi, This is obtained by the code run on esp as explained in the previous section)

n = urllib.request.urlopen(url).read() # get the raw html data in bytes (sends request and warn our esp8266)

n = n.decode("utf-8") # convert raw html bytes format to string :3

data = n.split() #split data we got. (if you programmed it to send more than one value) It splits them into separate list elements.

The variable “data” contains the data read from the ESP. After achieving this task, we can write the data in a text file using the write function in python.

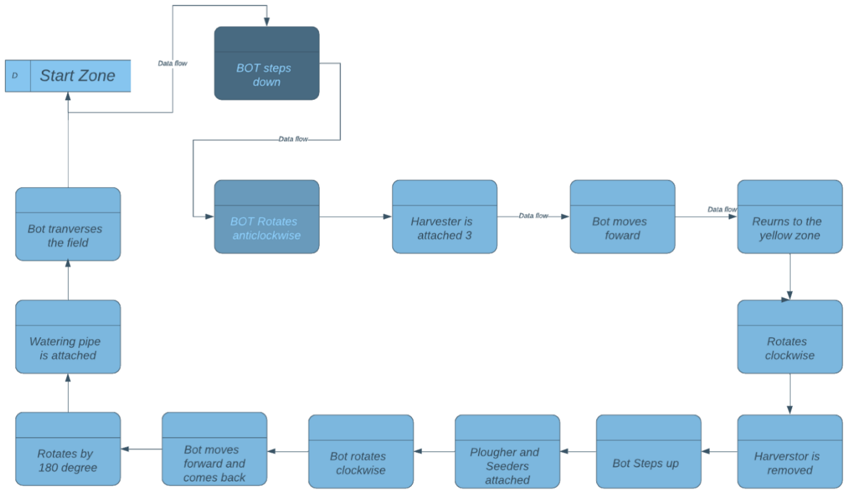
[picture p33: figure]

18

## Using Flask

Flask is a micro web framework written in python. Flask has been used in this project to render the web pages to a local host which can be accessed by the farmer. The sensor data stored in a local system cannot be directly read in the front end by any web pages and hence the necessity to read the data and render it to a local host. The flask reads the data of the particular node from the database and renders the data to the web page hosted on a local server.

## Solving the Problem Statement

Task flow for the navigation of the bot

Traversing

- Traversing occurs with the help of ultrasonic sensors. Which is used to maintain a constant distance from the wall.
- After starting, the bot will stop successively after a fixed distance and take readings of various sensors and water the zone accordingly.
- Ploughing will occur automatically as the bot moves.
- After detecting the end of the arena, the bot will take a 180 degree turn in the clockwise direction and move back to the respective starting zone.
- After detecting red or yellow region, bot will do the required action i.e. climbing up or down the steps.

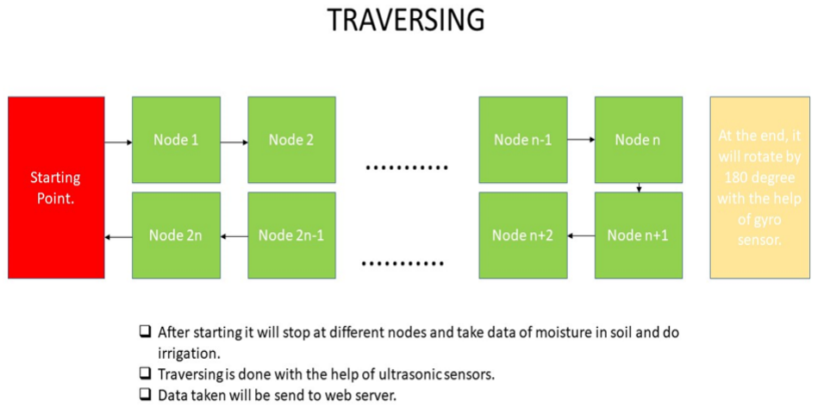
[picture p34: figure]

19

## Step Up Manoeuvre

- For climbing mechanism, 3 lead screws are actuated using 3 DC motors, which lift the whole body in 3 steps.
- In the first step, the whole body will be lifted by actuating the lead screws of middle and rear wheel assemblies. Then the bot will move forward until the front wheels rest above the step. A bump sensor will detect that the front wheels have touched the ground. The front colour sensor will detect the change in the zone for the prior part of the bot (yellow to red).
- In the second step, the Middle Wheels will be pulled back up and the bot will move forward to rest on the stair on front and middle wheels.
- In the last step, the back wheels will be pulled up and the bot would have climbed up.
- The step-down manoeuvre is the opposite of the step up manoeuvre.
- The bot also has an ability to lift itself above the crop for traversing in the field.

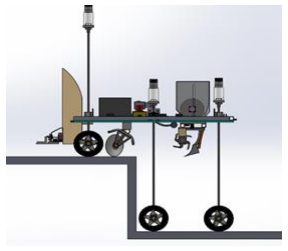
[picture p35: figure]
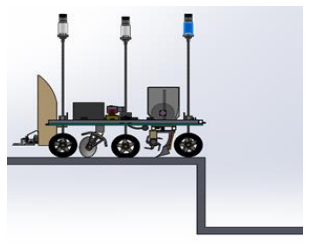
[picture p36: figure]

Fig.2: First step | Fig.3: Second step | Fig.4: third step

20

## Cost Structure

Component | Number used | Cost INR
Planetary Geared Motor | 4 | 19,996
Arduino Mega 2560 | 1 | 800
Node MCU Esp8266 | 1 | 260
Motor Driver | 6 | 15,000
Battery | 3 | 4997
Heavy Duty Wheels | 4 | 900
Caster Wheels | 4 | 200
Johnson motor | 5 | 1996
Rotary Encoder | 3 | 4497
Ultrasonic Sensor | 5 | 900
Mpu9250 | 1 | 190
Dht11 temperature | 1 | 108
Soil Moisture Sensor | 1 | 75
Bump Sensor | 4 | 400
Lead screw | 3 | 2397
Material for Body | ---- | 4000
Manufacturing | ---- | 3500
| | Total Cost- 60,216

21

## Proposal for real life solution

Apart from the technical solution as proposed in this report, there are some other serious measurements that needs to be undertaken by the government in order to ensure the smooth deployment of the bot.

1. A case study on Japan shows that in 1998 the country faced a steep decline in the percentage of hill farming, over 3.8 percent of the nation’s farming land was abandoned by 1998. This was due to the years of neglect and bias against the hill agriculture. The Japan government was able to realise the gravity of the solution and imposed strict measures to reverse the trend.
2. What has happened in Japan, carries a very important message for the future of hill agriculture in India. Looking deep inside the Uttarakhand hills, one finds that similar conditions is developing in several areas of the Indian Himalayas and that hill agriculture in India faces a similar situation sooner than later.
3. The government should impose a strategic turn around in its agricultural policies to revive the already declining hill farming. They should also provide subsidies on technological solution which tends to assist them. Our product also falls under this category. Surveys from Bhatta Gaon proves that farmers are willing to use modern equipment but they are incapable of affording the such solutions due to their already less income.

One of the key findings of the survey of Bhatta Gaon is that the height of the steps is very high ranging from 350cm to 480cm. The vertical surface of the steps is irregular and also slanted at an angle of about 5-10 degrees from the perpendicular. These conditions make it very difficult for any logical bot to navigate between the steps. The degree of manipulation in the bot to climb such high and irregular steps will decrease the overall efficiency and performance of the bot in performing other agricultural functions. The problem can be solved by customizing the steps of some degree so that the bot can perform efficiently that is to say that the steps can be modified to smaller height and regular terrain on the vertical wall.

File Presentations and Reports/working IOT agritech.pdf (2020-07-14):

Working of the IoT.

The reading from the different types of sensors (moisture, humidity, temperature etc) will be taken by a microcontroller and transferred wirelessly to a database. The readings will be stored in the database using file handling. The files with the reading will be sorted according to the nodes present on the field. A node is a region/area on the actual cultivated land whose details can be obtained in order to analyse the condition of the soil and the crops.

All the sensors are connected to the Arduino AT Mega microcontroller, which will be responsible for registering the input data from the sensors. Since Arduino AT-Mega does not have an in-built WiFi or Bluetooth system, so an ESP-8266 NODE-MCU can be used to transfer the data wirelessly to the database. The transfer of data from Arduino to the esp8266 can take place through interrupt pins, then the esp8266 will create a local server, another python script will run in the background on the same local server as created by the esp8266 which will, in turn, read the data from the esp8266 and store the received data in the database using file handling. The micro-header name ESP_MICRO.h is a very important header file needed for the esp8266 which is essential for the data transfer as described.

After the data is stored in the database in a sorted manner, we will need to render the files to the web page which will display the data to the user. The web page is thus an essential entity here. The web page contains a responsive replica of the land under cultivation. A basic snapshot of the web page looks like the picture as shown below.


The Web page Interface

The table on the right-hand side is the replica of the cultivated land and in our case is the arena for the problem statement. The table is responsive and will respond to the click of the user. Each step is divided into different nodes. It is the region where the Agritech bot will take the readings from the sensors. The user has to click on the particular nodes whose conditions/readings he wants to analyze. The details of the sensor reading will be displayed on the box present on the right-hand side of the web page. The data from the database will be rendered to the website using flask. A note/message can be delivered regarding what can be expected of the readings.

# Using Flask

Flask is a micro web framework written in python. Flask has been used in this project to render the web pages to a local host which can be accessed by the farmer. The sensor data stored in a local system cannot be directly read in the front end by any web pages and hence the necessity to read the data and render it to localhost. The flask reads the data of the particular node from the database and renders the data to the web page hosted on a local server.

A simplified flow chart of the process:-


One of the problems faced by the farmers in terrace farming is the lack of data from the land but this feature of the Agritech bot is the solution to the problem faced. The Agritech robot is envisioned to make the farmers smart, robust and decrease human dependency.

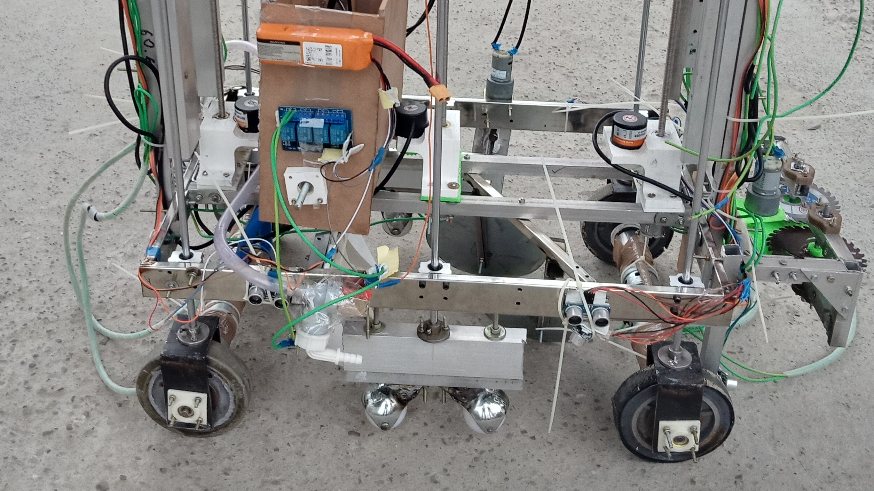
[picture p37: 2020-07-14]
Images and Videos/Images/Differential Chassis.jpg

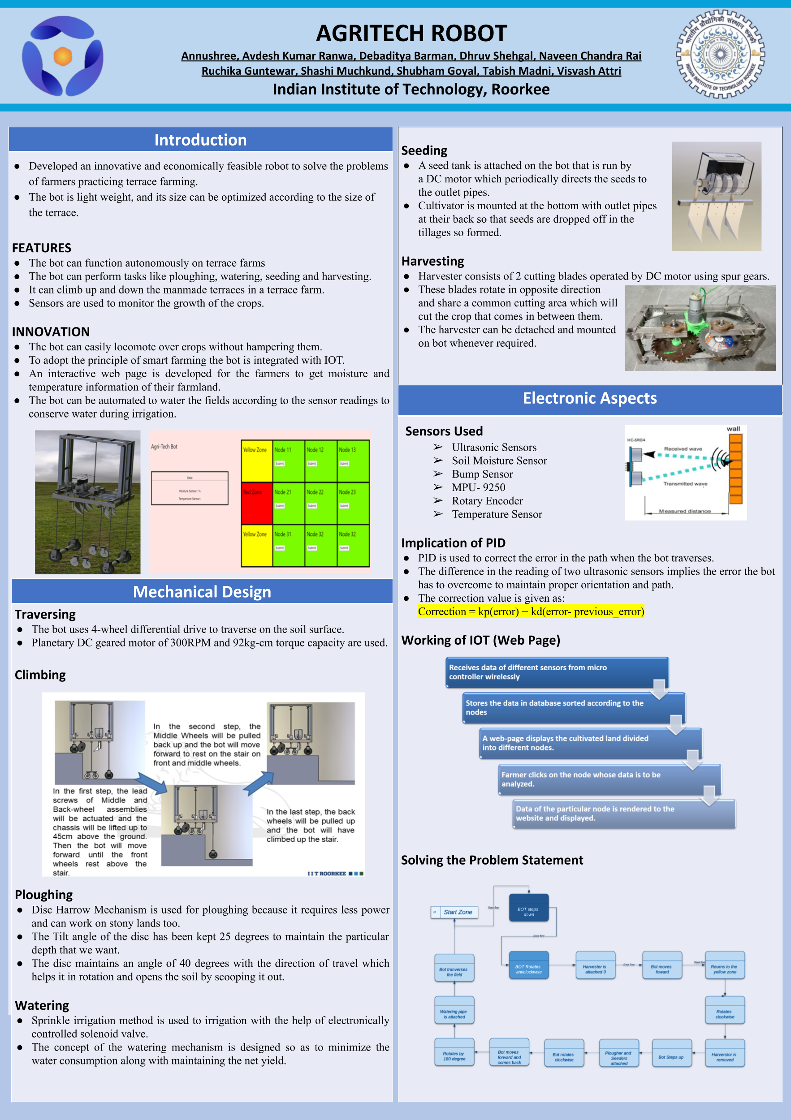
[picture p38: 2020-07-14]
Presentations and Reports/POSTER INTER IIT TECH.png

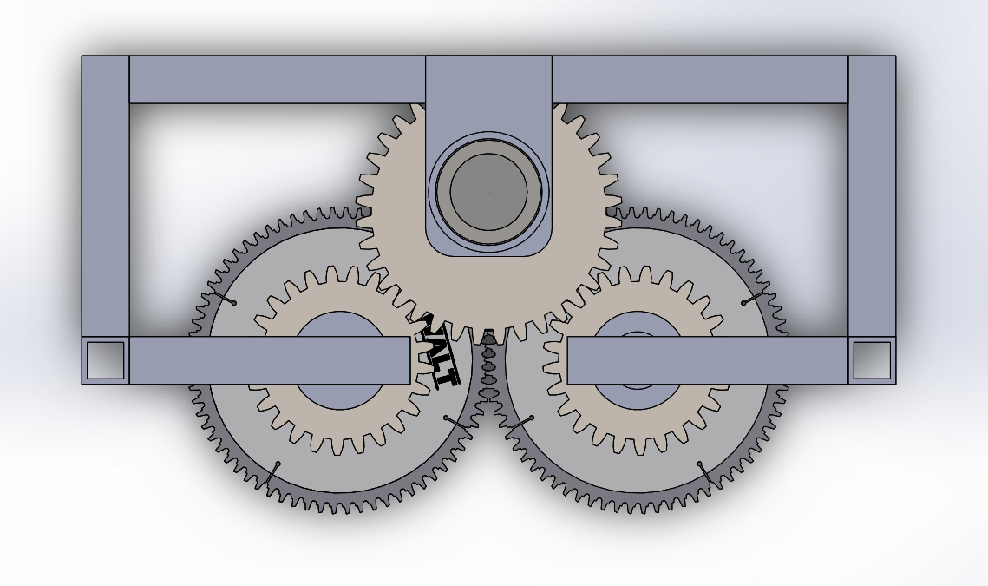
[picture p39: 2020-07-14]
Mechanical Design/CAD Images/Harvester Top View.PNG

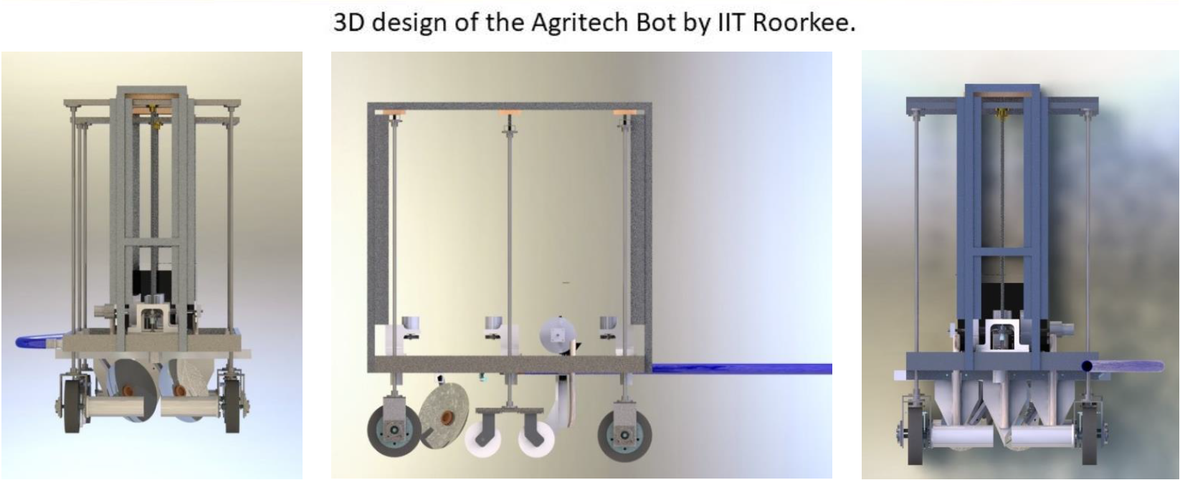
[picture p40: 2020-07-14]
Mechanical Design/CAD Images/Front View - Side View - Back View.PNG

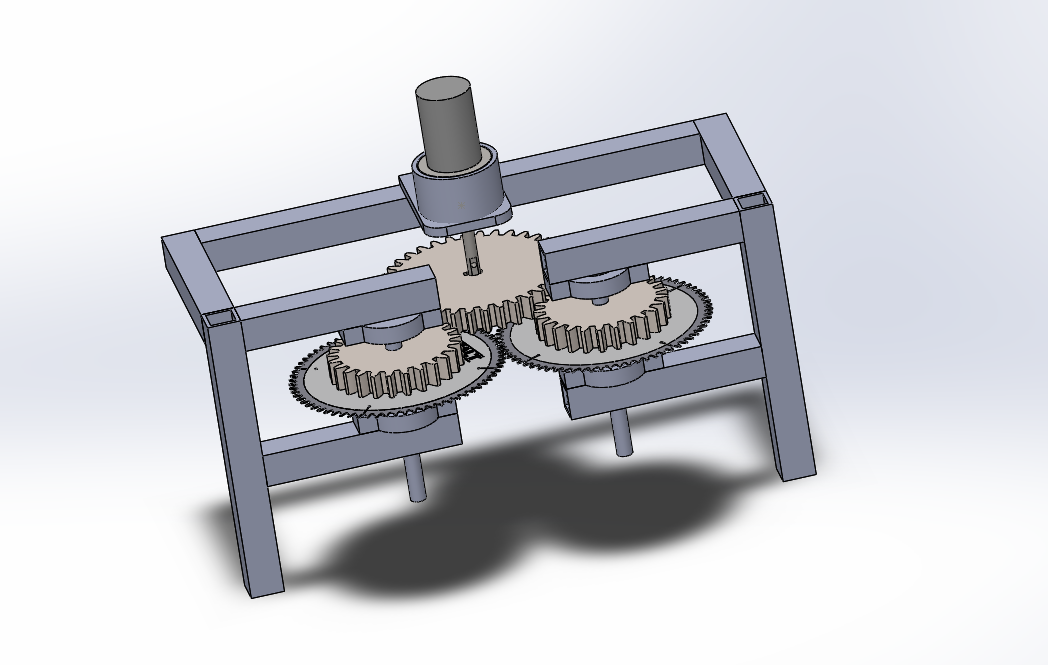
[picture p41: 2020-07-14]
Mechanical Design/CAD Images/Harvester Isometric Image.PNG

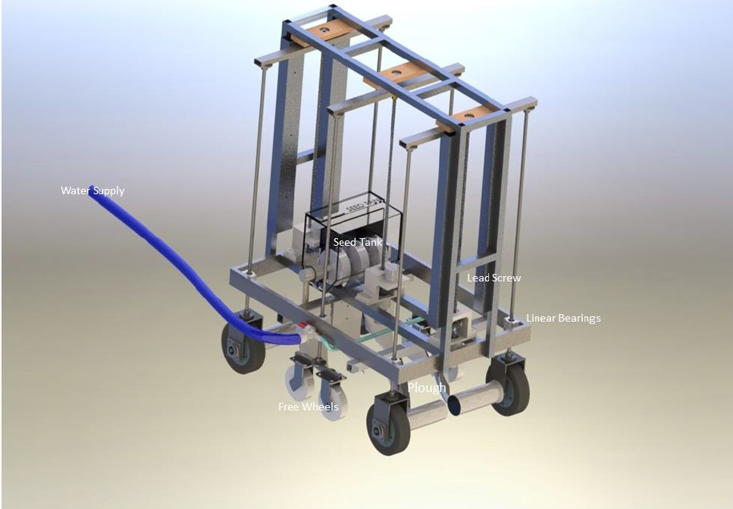
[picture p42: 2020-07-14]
Mechanical Design/CAD Images/Full Robot Isometric View.PNG

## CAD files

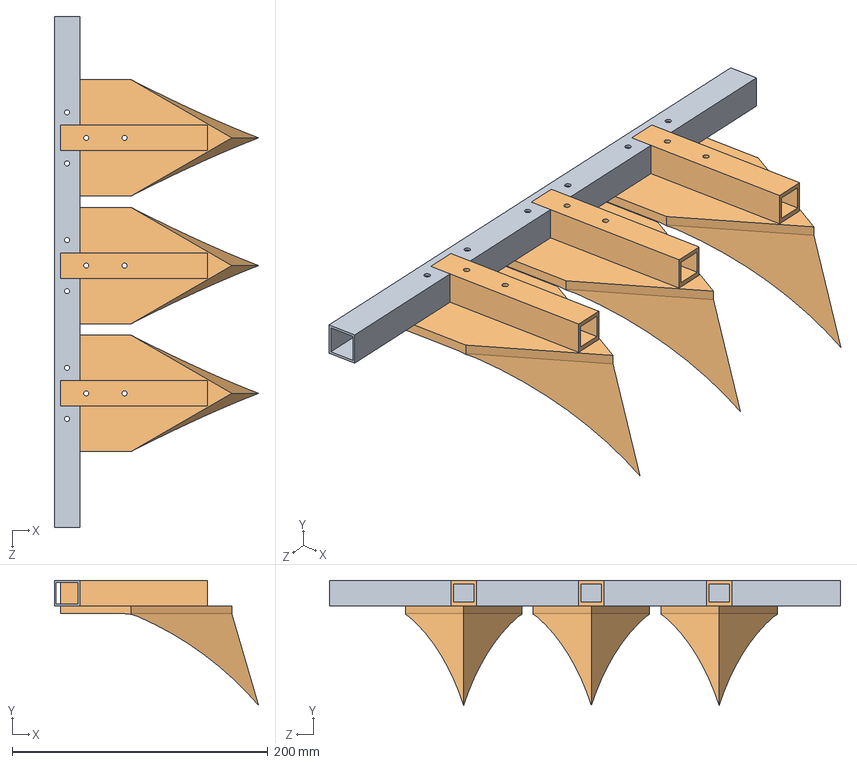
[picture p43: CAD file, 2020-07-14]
Mechanical Design/Solidworks Files/seeder assembly.SLDASM
160.0 x 98.0 x 400.0 mm
channel seeder
seeder x 3

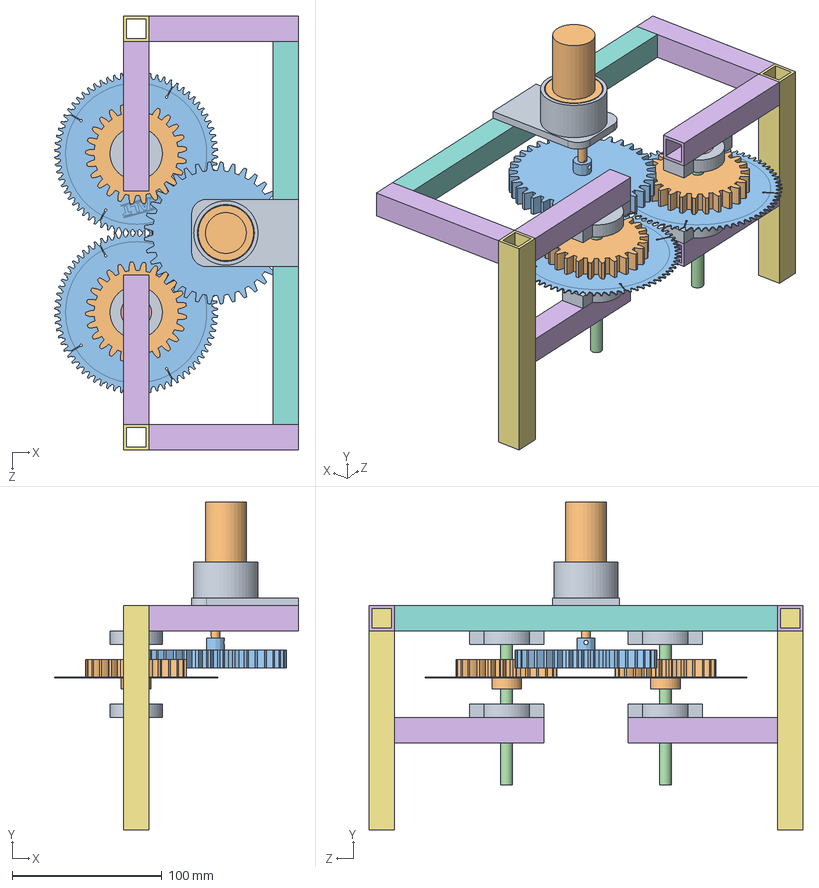
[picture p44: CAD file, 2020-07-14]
Mechanical Design/Solidworks Files/assembly.SLDASM
163.1 x 219.0 x 290.0 mm
bearing block hav x 4
spur gear_am x 2
Disco 14in 355mm 70 dentes x 2
rod 8mm hav x 2
bearing hav x 4
Al chennal hav x 6
Al chennal pre x 2
al channel c
mototr mounnt jonson hav
DC motor hav
motor gear1 hav

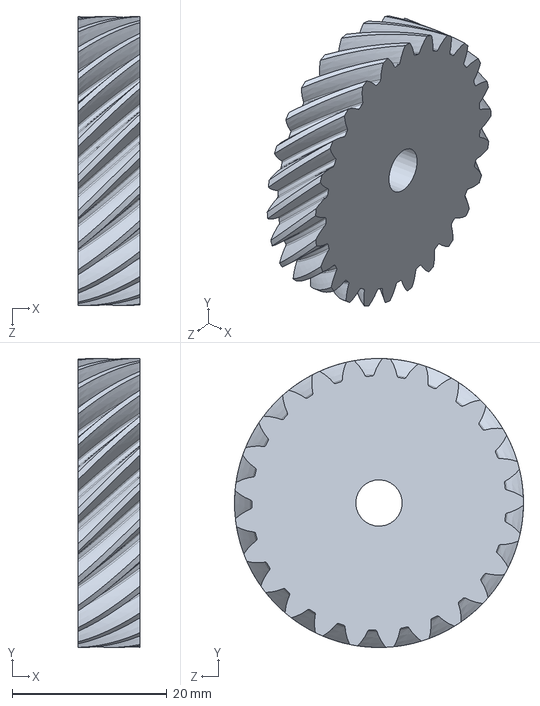
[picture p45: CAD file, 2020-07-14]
Mechanical Design/Solidworks Files/helical GEAR assem.SLDASM
8.00 x 37.4 x 37.4 mm

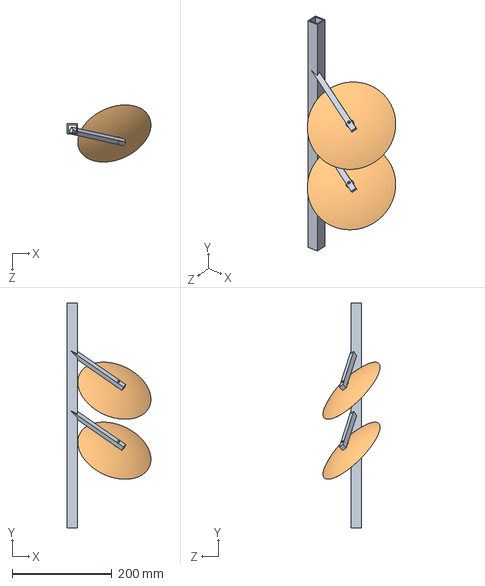
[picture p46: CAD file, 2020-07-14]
Mechanical Design/Solidworks Files/Plough assembly.SLDASM
167.8 x 450.0 x 114.3 mm
base plough
FRONTAL BLADE SET plough x 2

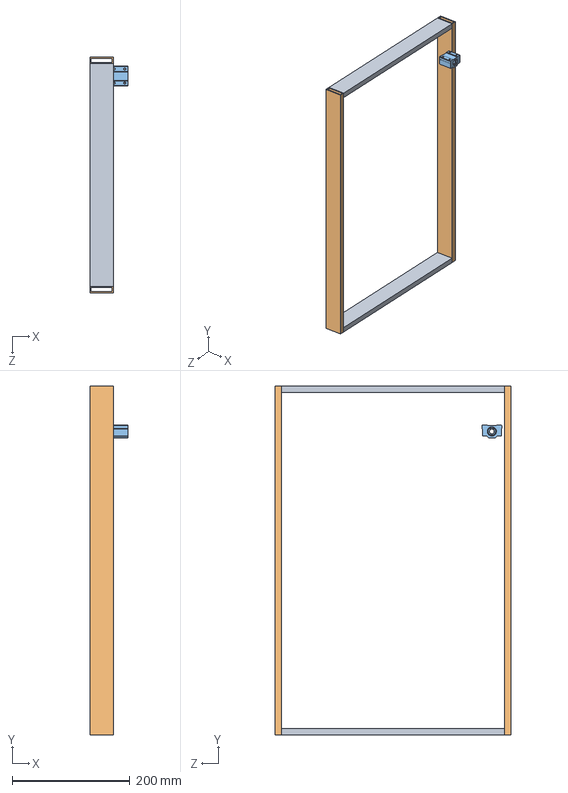
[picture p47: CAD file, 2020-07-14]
Mechanical Design/Solidworks Files/Assem1.SLDASM
65.3 x 592.0 x 400.0 mm
38 CM steel channel x 2
59CM steel channel x 2
Linear Bearing, 8mm Shaft

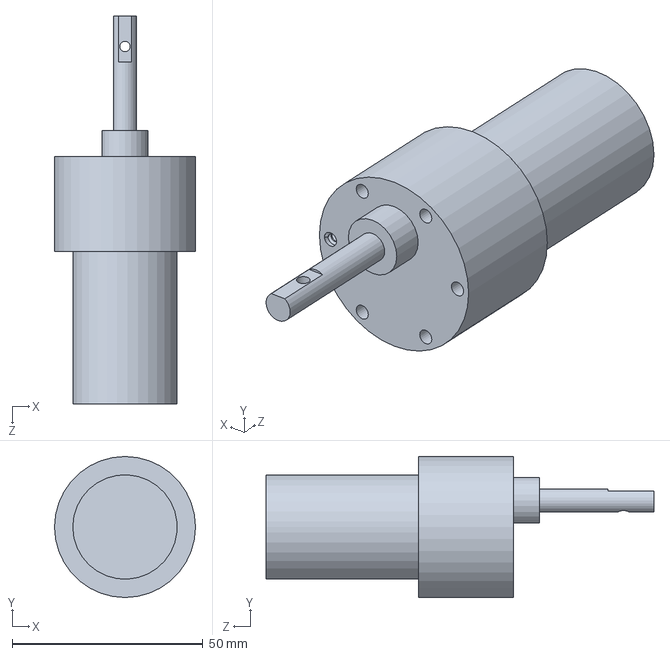
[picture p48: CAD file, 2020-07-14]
Mechanical Design/Solidworks Files/DC motor hav.SLDPRT
37.0 x 37.0 x 101.8 mm

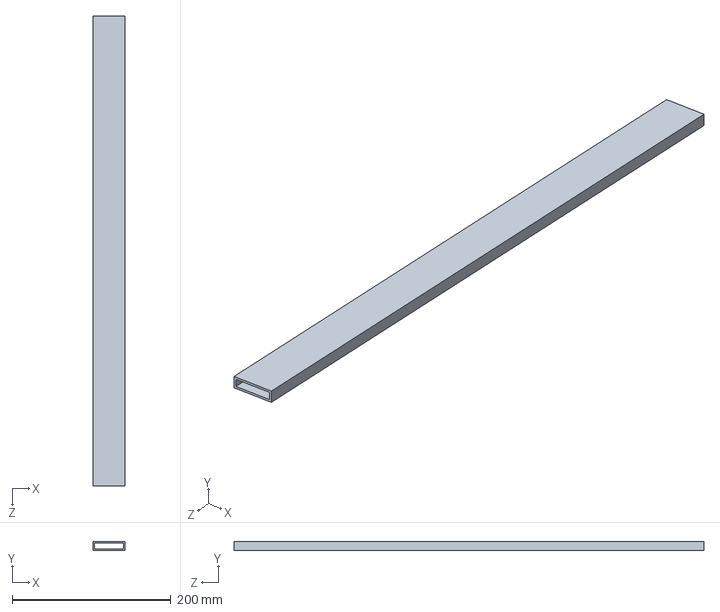
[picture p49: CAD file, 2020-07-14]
Mechanical Design/Solidworks Files/59CM steel channel.SLDPRT
40.0 x 11.0 x 592.0 mm

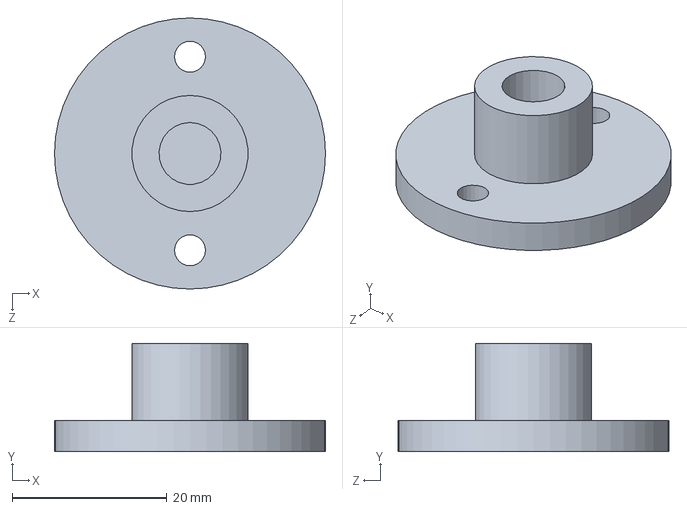
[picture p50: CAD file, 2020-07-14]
Mechanical Design/Solidworks Files/Rod Welding Mount.SLDPRT
35.0 x 14.0 x 35.0 mm

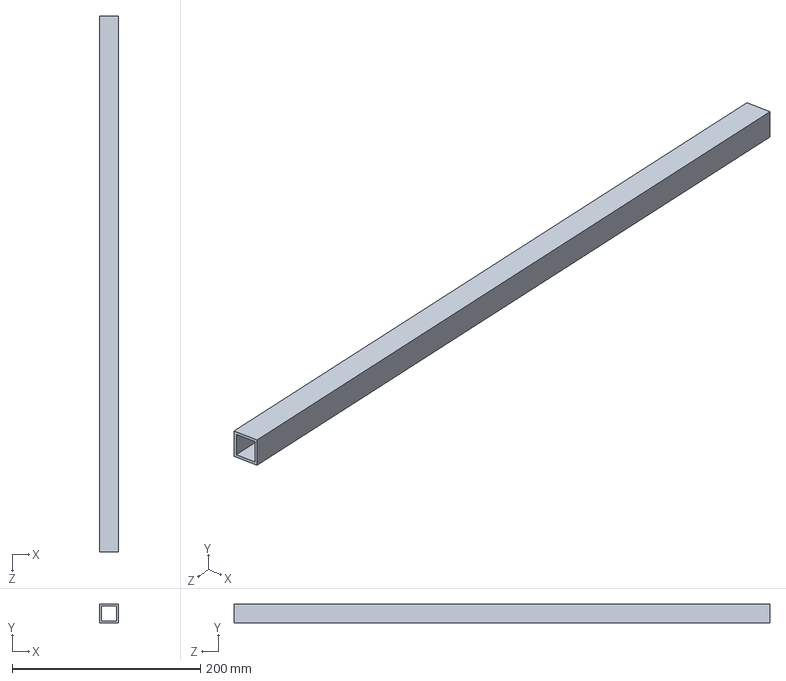
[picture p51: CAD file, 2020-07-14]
Mechanical Design/Solidworks Files/Support channel middle base.SLDPRT
20.0 x 20.0 x 570.0 mm

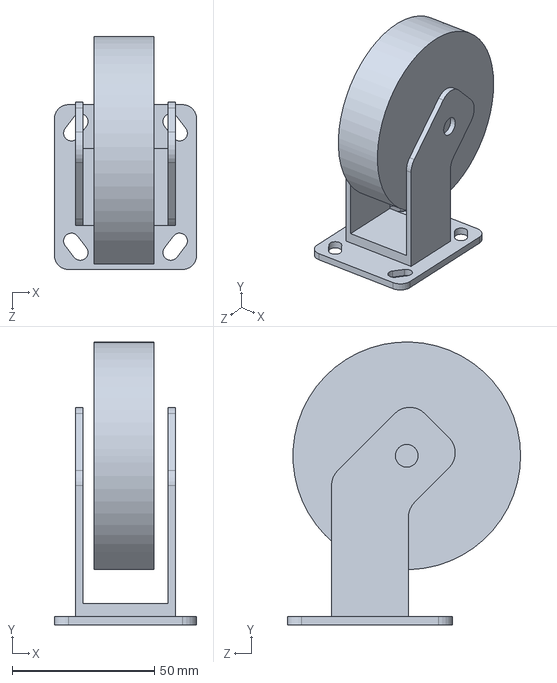
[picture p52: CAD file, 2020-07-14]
Mechanical Design/Solidworks Files/Wheel idler.SLDPRT
50.0 x 99.4 x 81.9 mm

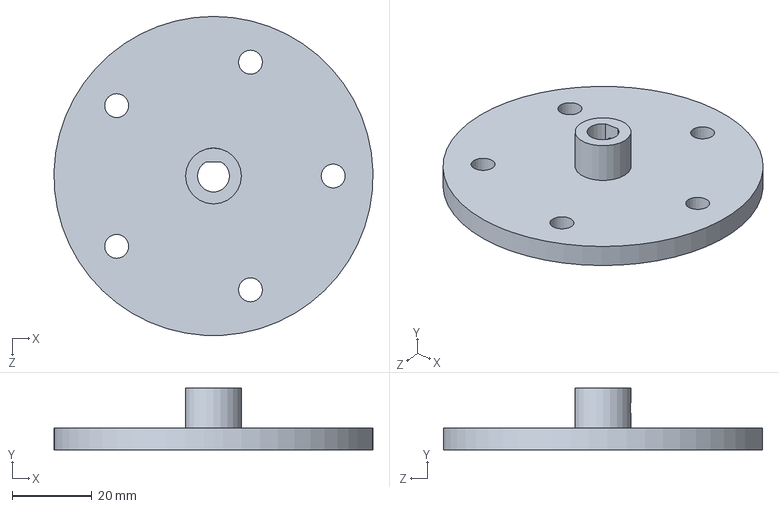
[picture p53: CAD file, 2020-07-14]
Mechanical Design/Solidworks Files/wheel coupling.SLDPRT
80.0 x 15.5 x 80.0 mm

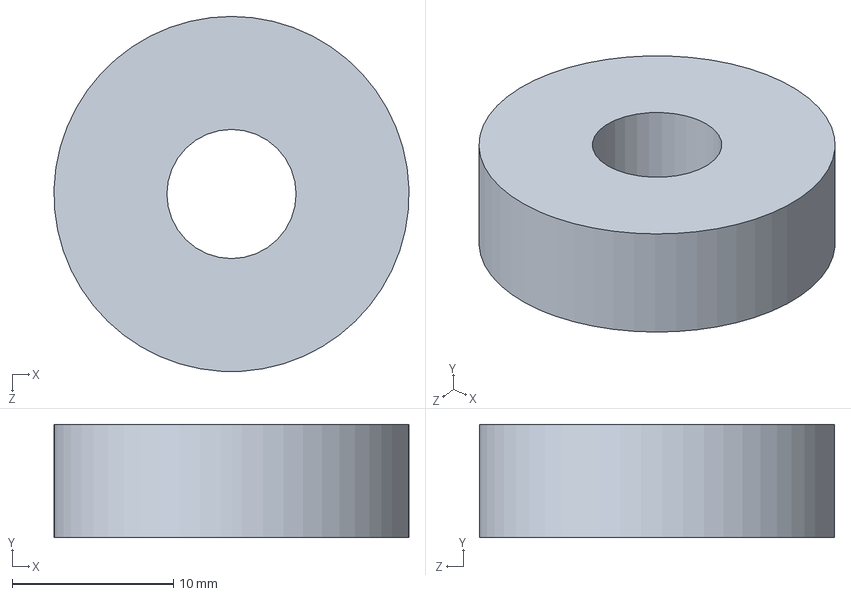
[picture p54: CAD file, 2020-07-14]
Mechanical Design/Solidworks Files/8mm Ball Bearing.SLDPRT
22.0 x 7.00 x 22.0 mm

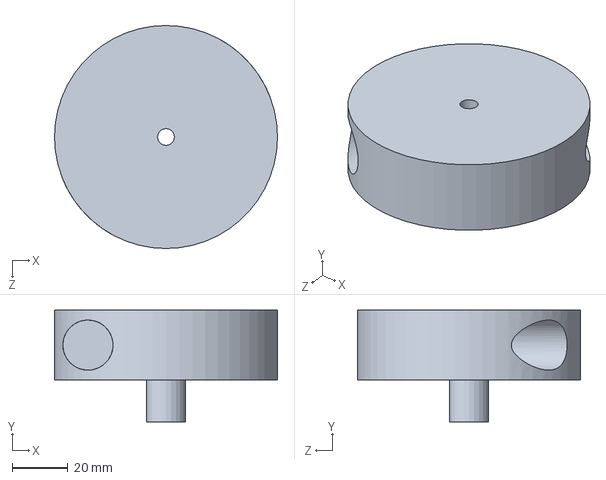
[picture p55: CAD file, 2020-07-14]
Mechanical Design/Solidworks Files/SEEDER Rotator.SLDPRT
80.0 x 40.0 x 80.0 mm

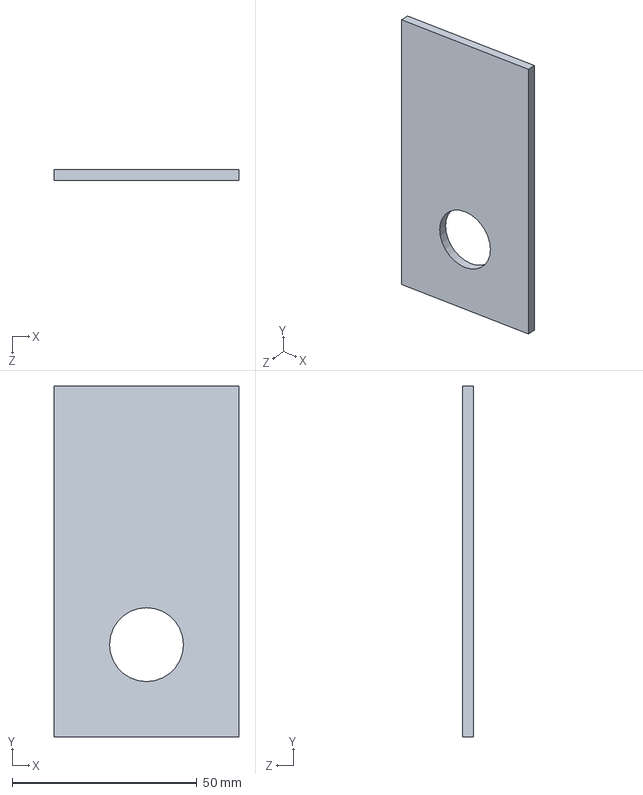
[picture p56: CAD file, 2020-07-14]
Mechanical Design/Solidworks Files/WHEEL Plate 3mm Bearing.SLDPRT
50.0 x 95.0 x 3.00 mm

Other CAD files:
Mechanical Design/Solidworks Files/Lead Support Connecting channel.SLDPRT
Mechanical Design/Solidworks Files/DC motor Clamp UP.SLDPRT
Mechanical Design/Solidworks Files/steel channel 60cm.SLDPRT
Mechanical Design/Solidworks Files/mototr mounnt jonson hav.SLDPRT
Mechanical Design/Solidworks Files/38 CM steel channel.SLDPRT
Mechanical Design/Solidworks Files/Al channel LeadScrew support.SLDPRT
Mechanical Design/Solidworks Files/Al chennal hav.SLDPRT
Mechanical Design/Solidworks Files/Al chennal pre.SLDPRT
Mechanical Design/Solidworks Files/Ball bearing 6mm.SLDPRT
Mechanical Design/Solidworks Files/Bearing Block Johnson's motor.SLDPRT
Mechanical Design/Solidworks Files/Bearing block Lead Screw up.SLDPRT
Mechanical Design/Solidworks Files/DC 3D washer.SLDPRT
Mechanical Design/Solidworks Files/DC LeadScrew 900Rpm.SLDPRT
Mechanical Design/Solidworks Files/DC Motor.SLDPRT
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

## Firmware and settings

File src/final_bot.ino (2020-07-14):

long Time, Time1 = 0;
bool auto_mode=0;
bool manual_mode=1;
bool seeder1=0;
bool harvester1=0;
int value_fbump=0;
int value_mbump=0;
int value_bbump=0;
int manual_speed=90;


int harvester = 40;
int pwm_harvester = 8;

int seeder = 38;
int pwm_seeder = 5;

int sensor = 40;
int pwm_sensor = 8;

int main_state=0;

int solenoid = 38;
int x=47,y=35,z=37,r=25,d=23;
int internal_sensor=0;



/////////////////////////GYRO////////////////////////
#include <MPU9250.h>

MPU9250 IMU;
int sig = 7;
int16_t gyro[3] = {0, 0, 0};
int16_t acc[3] = {0, 0, 0};
float gyroBias[3]  = {0, 0, 0};
float accelBias[3] = {0, 0, 0};
int dt;
long Time_gyro;
double s=0;
double angle = 00.00;
double first_reading=0;
double correction = 0;
double angle_kp = 2.5, angle_kd = 3.9;

int p = 0;
int time0 = 0;

double t;
double angle_error = 0, angle_derror = 0, angle_perror = 0, angle_correction = 0;

void getgyro()
{
  
  IMU.readGyroData(gyro);
  dt = micros() - Time_gyro;

  angle += (gyro[2]-s)*dt/131.0/1000000.0;
  Time_gyro = micros();
  Serial.println("angle=");
  Serial.println(angle);
}



/////////////////////////////ULTRA///////////////////////////////


#include <NewPing.h>
#define SONAR_NUM 8
#define MAX_DISTANCE 75
#define PING_INTERVAL 20

unsigned long pingTimer[SONAR_NUM]; // When each pings.
unsigned int ultradistance[SONAR_NUM]; // Store ping distances.
uint8_t currentSensor = 0; // Which sensor is active.

int frdistance = 0, fldistance = 0, topdistance = 0, brdistance = 0, front_height, middle_height, back_height ,  bldistance = 0;

double velocity_correction = 0, kp_velocity = 2.3, velocity_error = 0, kd_velocity = 2.7, velocity_derror = 0, velocity_perror = 0;
double dis_correction = 0, kp_dis = 2, dis_error = 0, kd_dis = 3.5, dis_derror = 0, dis_perror = 0;

NewPing sonar[SONAR_NUM] =
{ // Sensor object array.
  NewPing(A3, A2, MAX_DISTANCE),
  NewPing(A4, A5, MAX_DISTANCE),
  NewPing(A8, A9, MAX_DISTANCE),
  NewPing(A6, A7 , MAX_DISTANCE),
  NewPing(A0, A1, MAX_DISTANCE),
  NewPing(A14, A15, MAX_DISTANCE),
  NewPing(A12, A13 , MAX_DISTANCE),
  NewPing(44, 46, MAX_DISTANCE),

};
void pingdistance()
{

  for (uint8_t i = 0; i < SONAR_NUM; i++)
  {
    if (millis() >= pingTimer[i]) {
      pingTimer[i] += PING_INTERVAL * SONAR_NUM;
      if (i == 0 && currentSensor == SONAR_NUM - 1)
      {
        oneSensorCycle();
      } // Do something with results.
      sonar[currentSensor].timer_stop();
      currentSensor = i;
      ultradistance[currentSensor] = 0;
      sonar[currentSensor].ping_timer(echoCheck);
    }

  }

}
void echoCheck()
{ // If ping echo, set distance to array.
  if (sonar[currentSensor].check_timer())
    ultradistance[currentSensor] = sonar[currentSensor].ping_result / US_ROUNDTRIP_CM;

}

void oneSensorCycle()
{ // Do something with the results.
  fldistance = ultradistance[0];
  topdistance = ultradistance[1];
  frdistance = ultradistance[2];
  brdistance = ultradistance[3];
  bldistance = ultradistance[4];
  front_height = ultradistance[7];
  middle_height = ultradistance[6];
  back_height = ultradistance[5];

  for (uint8_t i = 0; i < SONAR_NUM; i++) {
    Serial.print(i);
    Serial.print("=");
    Serial.print(ultradistance[i]);
    Serial.println("cm ");
  }

}

///////////////////////WHEEL_MOTOR///////////////////////

double v1 = 0, v2 = 0, v3 = 0, v4 = 0;

int fr = 26;
int pwm1 = 4;
int fl = 43;
int pwm2 = 12;
int br = 32;
int pwm3 = 7;
int bl = 41;
int pwm4 = 11;


void backwheel_forward(int a,int b)
{
  digitalWrite(br, HIGH);
  analogWrite(pwm3, a);
  digitalWrite(bl, HIGH);
  analogWrite(pwm4, b);
}


///////////////////////////////////////////////////////////////////////

void backwheel_backward()
{
  digitalWrite(br, LOW);
  analogWrite(pwm3, 40);
  digitalWrite(bl, LOW);
  analogWrite(pwm4, 40);
}


///////////////////////////////////////

void frontwheel_forward(int a, int b)
{
  digitalWrite(fr, HIGH);
  analogWrite(pwm1, a);
  digitalWrite(fl, HIGH);
  analogWrite(pwm2, b);
}


////////////////////////////////////////

void frontwheel_backward()
{
  digitalWrite(fr, LOW);
  analogWrite(pwm1, 40);
  digitalWrite(fl, LOW);
  analogWrite(pwm2, 40);
}




////////////////////////////////LEADMOTORS///////////////////////////////////////

int lead_bm_error = 0, lead_bm_perror = 0, lead_bm_derror = 0, correction_lead_bm = 0;
double kp_lead_bm = 0.005, kd_lead_bm = 0;
int upstair_state = 0, variable = 0;

int lead_bf_error = 0, lead_bf_perror = 0, lead_bf_derror = 0, correction_lead_bf = 0;
double kp_lead_bf = 0.005, kd_lead_bf = 0;
int downstair_state = 0;

double m_pwm = 0, b_pwm = 0, f_pwm = 0;

int f = 40;
int pwmf = 8;
#define a1 19
#define b1  A11
float theta1c = 0;
long int temp1, counter1 = 0;


int m = 38;
int pwmm = 5;
#define a2 18
#define b2  A10
float theta2c = 0;
long int temp2, counter2 = 0;


int b = 49;
int pwmb = 6;
int lead1=40;
int lead1_pwm=8;
int lead2=40;
int lead2_pwm=8;
int lead_speed=150;
#define a3 2
#define b3  3
float theta3c = 0;
long int temp3, counter3 = 0;

int lead_bf_error_up = 0, lead_bf_perror_up = 0, lead_bf_derror_up = 0, correction_lead_bf_up = 0;
double kp_lead_bf_up = 0.005, kd_lead_bf_up = 0;
void pid_bf_lead_up()
{
  lead_bf_error_up = counter1 - counter3;
  lead_bf_derror_up = lead_bf_error_up - lead_bf_perror_up;
  correction_lead_bf_up = kp_lead_bf_up * lead_bf_error_up + kd_lead_bf_up * lead_bf_derror_up;
  lead_bf_perror_up = lead_bf_derror_up;
  b_pwm =200-correction_lead_bf_up;
  f_pwm =200 +correction_lead_bf_up;

  if(b_pwm>255){
    b_pwm=255;
  }
  if(b_pwm<0){
    b_pwm=0;
    }
      if(f_pwm>255){
    f_pwm=255;
  }
  if(f_pwm<0){
    f_pwm=0;
    }
  }
void pid_bm_lead()
{
  lead_bm_error = counter3 - counter2;
  lead_bm_derror = lead_bm_error - lead_bm_perror;
  correction_lead_bm = kp_lead_bm * lead_bm_error + kd_lead_bm * lead_bm_derror;
  lead_bm_perror = lead_bm_derror;
  b_pwm = 111 - correction_lead_bm;
  m_pwm = 220 + correction_lead_bm;
    if(b_pwm>255){
    b_pwm=255;
  }
  if(b_pwm<0){
    b_pwm=0;
    }
      if(m_pwm>255){
    m_pwm=255;
  }
  if(m_pwm<0){
    m_pwm=0;
    }
}

void pid_bf_lead()
{
  lead_bf_error = counter3 - counter1;
  lead_bf_derror = lead_bf_error - lead_bf_perror;
  correction_lead_bf = kp_lead_bf * lead_bf_error + kd_lead_bf * lead_bf_derror;
  lead_bf_perror = lead_bf_derror;
  b_pwm = 111 - correction_lead_bf;
  f_pwm = 110 + correction_lead_bf;
    if(b_pwm>255){
    b_pwm=255;
  }
  if(b_pwm<0){
    b_pwm=0;
    }
      if(f_pwm>255){
    f_pwm=255;
  }
  if(f_pwm<0){
    f_pwm=0;
    }
}

void ai2() {
  if (digitalRead(b2) == !digitalRead(a2))
  {
    counter2--;
  } else {
    counter2++;
  }
}

////////////////////////////////////////////////////////////////////////////

void ai1() {
  if (digitalRead(b1) == !digitalRead(a1))
  {
    counter1++;
  } else {
    counter1--;
  }
}


/////////////////////////////////////////////////////////////////////////////


void ai3() {
  if (digitalRead(b3) == !digitalRead(a3))
  {
    counter3++;
  } else {
    counter3--;
  }
}

//////////////////////////////////////////////////////////////////////////////




void middle_lead_up(int b)
{
  digitalWrite(m, HIGH);
  analogWrite(pwmm, b);
}


/////////////////////////////////////////////////
void middle_lead_down(int a)
{
  digitalWrite(m, LOW);
  analogWrite(pwmm, a);
}

//////////////////////////////////////////////////
void front_lead_up(int c)
{
  digitalWrite(f, HIGH);
  analogWrite(pwmf, c);
}

/////////////////////////////////////////////////////////////////
void front_lead_down(int d)
{
  digitalWrite(f, LOW);
  analogWrite(pwmf, d);
}

///////////////////////////////////////////////////////////////////

void back_lead_up(int e)
{
  digitalWrite(b, HIGH);
  analogWrite(pwmb, e);
}

////////////////////////////////////////////////////////////////////////
void back_lead_down(int f)
{
  digitalWrite(b, LOW);
  analogWrite(pwmb, f);
}





////////////////////////////////////////////////////////////


void stopbot()
{
  analogWrite(pwm2, 0);
  analogWrite(pwm1, 0);
  analogWrite(pwm3, 0);
  analogWrite(pwm4, 0);
  analogWrite(pwmm, 0);
  analogWrite(pwmb, 0);
  analogWrite(pwmf, 0);
}

#include <PS3BT.h>



#include <usbhub.h>
// Satisfy the IDE, which needs to see the include statment in the ino too.
#ifdef dobogusinclude
#include <spi4teensy3.h>
#include <SPI.h>
#endif






//////////////    PS3
USB Usb;

//(PS3BT)
BTD Btd(&Usb); // You have to create the Bluetooth Dongle instance like so
///* You can create the instance of the class in two ways */
//PS3BT PS3(&Btd); // This will just create the instance
PS3BT PS3(&Btd, 0x00, 0x1B, 0x10, 0x00, 0x17, 0xD9);
void setup()
{
 
Serial.begin(9600);//

  ps3_init();
  pingTimer[0] = millis() + 30; //first ping start in ms
  for (uint8_t i = 1; i < SONAR_NUM; i++)
    pingTimer[i] = pingTimer[i - 1] + PING_INTERVAL;
  while (millis() < 2000)
  {
    pingdistance();
  }
    for(int i=0;i<1000;i++)
  { IMU.readGyroData(gyro);
    
    s+=gyro[2];
  }
  s=s/1000;

   IMU.readGyroData(gyro);
  dt = micros() - Time;
  angle += (gyro[2]-s)*dt/131.0/1000000.0;
  Time = micros();
  first_reading=angle;  
//  Serial.println("fr");
//  Serial.println(first_reading);
   angle=angle-first_reading;
   
  Serial3.begin(115200);
   

  pinMode(fr, OUTPUT);
  pinMode(pwm1, OUTPUT);
  pinMode(fl, OUTPUT);
  pinMode(pwm2, OUTPUT);
  pinMode(br, OUTPUT);
  pinMode(pwm3, OUTPUT);
  pinMode(bl, OUTPUT);
  pinMode(pwm4, OUTPUT);
  pinMode(sig, OUTPUT);

  pinMode(f_bump, INPUT); //bump
  pinMode(m_bump, INPUT); //bump
  pinMode(b_bump, INPUT); //bump

  pinMode(a1, INPUT_PULLUP);
  pinMode(b1, INPUT_PULLUP);
  pinMode(f, OUTPUT);
  pinMode(pwmf, OUTPUT);
  pinMode(a2, INPUT_PULLUP);
  pinMode(b2, INPUT_PULLUP);
  pinMode(m, OUTPUT);
  pinMode(pwmm, OUTPUT);
  pinMode(a3, INPUT_PULLUP);
  pinMode(b3, INPUT_PULLUP);
  pinMode(b, OUTPUT);
  pinMode(pwmb, OUTPUT);
  attachInterrupt(digitalPinToInterrupt(a1), ai1, CHANGE);
  attachInterrupt(digitalPinToInterrupt(a2), ai2, CHANGE);
  attachInterrupt(digitalPinToInterrupt(a3), ai3, CHANGE);

  pinMode(x,INPUT_PULLUP);
  pinMode(y,INPUT_PULLUP);
  pinMode(z,INPUT_PULLUP);
  pinMode(r,INPUT_PULLUP);
  pinMode(d,INPUT_PULLUP);
  pinMode(solenoid,OUTPUT);
  digitalWrite(solenoid,HIGH);
}


int number_harvestor = 0;


void correctangle()
{
  getgyro();
  angle_error = angle;
  angle_derror = angle_error  - angle_perror ;
  angle_perror = angle_error ;
  angle_correction = angle_kp * angle_perror + angle_kd * angle_derror;
  Serial.println("angle_correction");
  Serial.println(angle_correction);

}

void correctultra()
{
  if (fldistance > 0 && bldistance > 0 && number_harvestor == 0)
  {
    velocity_error = int((bldistance) - (fldistance));
    velocity_derror = velocity_error - velocity_perror;
    velocity_correction = kp_velocity * velocity_error + kd_velocity * velocity_derror;
    velocity_perror = velocity_error;

    dis_correction = 0;
    dis_error = 10 - (int(fldistance + bldistance) / 2);
    dis_derror = dis_error - dis_perror;
    dis_correction = kp_dis * dis_error + kd_dis * dis_derror;
    dis_perror = dis_error;
  }
  else if (frdistance > 0 && brdistance > 0 && number_harvestor == 1)
  {
    velocity_error = int(frdistance) - (brdistance);
    velocity_derror = velocity_error - velocity_perror;
    velocity_correction = kp_velocity * velocity_error + kd_velocity * velocity_derror;
    velocity_perror = velocity_error;

    dis_correction = 0;
    dis_error = -50 + (int(frdistance + brdistance) / 2);
    dis_derror = dis_error - dis_perror;
    dis_correction = kp_dis * dis_error + kd_dis * dis_derror;
    dis_perror = dis_error;
  }
//  Serial.print("velerror=");
//  Serial.println(velocity_error);
//  Serial.print("disterror=");
//  Serial.println(dis_error);
}

void straight()
{
//  Serial.println("abcde3");
  //    if(angle!=0)
  //    {
  correctangle();
  //    }
  correctultra();
  correction = (angle_correction + velocity_correction) / 2;
  Serial.println("correction");
  Serial.println(correction);

  v1 = 120 - correction - dis_correction; //110
  v2 = 120+ correction + dis_correction;
  v3 = 120 - correction - dis_correction; //100
  v4 = 120 + correction + dis_correction; //100


  if (v3 > 255) {
    v3 = 255;
  }
  if (v4 > 255) {
    v4 = 255;
  }
  if (v1 > 255) {
    v1 = 255;
  }
  if (v2 > 255) {
    v2 = 255;
  }
  if (v3 < 0) {
    v3 = 0;
  }
  if (v4 < 0) {
    v4 = 0;
  }
  if (v1 < 0) {
    v1 = 0;
  }
  if (v2 < 0) {
    v2 = 0;
  }
  //    Serial.println("v1");
  //    Serial.println(v1);
  //    Serial.println("v2");
  //    Serial.println(v2);
  //    Serial.println("v3");
  //    Serial.println(v3);
  //    Serial.println("v4");
  //    Serial.println(v4);
frontwheel_forward(v1,v2);
backwheel_forward(v3,v4);
}

void rotateleft(int b)
{
  //   Serial.println("xyz");
  getgyro();
  if (angle < 30)
  {
    digitalWrite(fr, HIGH);
    analogWrite(pwm1, 100);
    digitalWrite(br, HIGH);
    analogWrite(pwm3, 100);
    digitalWrite(fl, LOW);
    analogWrite(pwm2, 40);
    digitalWrite(bl, LOW);
    analogWrite(pwm4, 40);
  }
  else if (angle >= 30 && angle <= b)
  {
    digitalWrite(fr, HIGH);
    analogWrite(pwm1, 130);
    digitalWrite(br, HIGH);
    analogWrite(pwm3, 130);
    digitalWrite(fl, LOW);
    analogWrite(pwm2, 100);
    digitalWrite(bl, LOW);
    analogWrite(pwm4, 100);
  }

}

void rotateright(int a,int b)
{
//  Serial.println("xyz");
  getgyro();
  if (angle > a)
  {
    digitalWrite(fl, HIGH);
    analogWrite(pwm2, 100);
    digitalWrite(bl, HIGH);
    analogWrite(pwm4, 100);
    digitalWrite(fr, LOW);
    analogWrite(pwm1, 40);
    digitalWrite(br, LOW);
    analogWrite(pwm3, 40);
  }
  else if (angle <= a && angle >= b)
  {
    digitalWrite(bl, HIGH);
    analogWrite(pwm4, 130);
    digitalWrite(fl, HIGH);
    analogWrite(pwm2, 130);
    digitalWrite(fr, LOW);
    analogWrite(pwm1, 100);
    digitalWrite(br, LOW);
    analogWrite(pwm3, 100);
  }

}


 
int number_seeder = 0;


int number_sensor=0;

 

 
void loop()
{
Serial.print(manual_mode);
Serial.print("   ");
Serial.println(auto_mode);
ps3();//
//check_ps3();
if(PS3.getButtonClick(L1)&&harvester1==0)
{
  harvester1=1;
  }
  else if(PS3.getButtonClick(L1)&& harvester1==1)
  {
    harvester1=0;}
    if(harvester1==0)
    {
      digitalWrite(f,HIGH);
      analogWrite(pwmf,0);
      }
      else if (harvester1==1)
      {
       digitalWrite(f,HIGH);
      analogWrite(pwmf,100); }
      if(PS3.getButtonClick(R1)&&seeder1==0)
{
 seeder1=1;
  }
  else if(PS3.getButtonClick(R1)&& seeder1==1)
  {
    seeder1=0;}
    if(seeder1==0)
    {
      digitalWrite(b,HIGH);
      analogWrite(pwmb,0);
      }
      else if (seeder1==1)
      {
       digitalWrite(b,HIGH);
      analogWrite(pwmb,100); }
      

if (PS3.getButtonClick(SELECT)&&manual_mode==0)
{
  manual_mode=1;
  auto_mode=0;
  }
 else if (PS3.getButtonClick(START)&&manual_mode==1)
{
  manual_mode=0;
  auto_mode=1;
  }
  if(auto_mode==1&&manual_mode==0)
  {
  value_fbump=digitalRead(f_bump);
  value_bbump=digitalRead(b_bump);
  value_mbump=digitalRead(m_bump);
  pingdistance();

 if(digitalRead(d)==LOW )
  {
   // Serial.println("downstair");
     downstair();
     
  }

   else if(digitalRead(y)==LOW)
  {
     //Serial.println("upstair");
    upstair();
  }
    else if( digitalRead(z)==LOW)
  {
     //Serial.println("wallfollowseeder");
    wallfollow_seeder();
  }
      else if(digitalRead(x)==LOW)
  {
    //Serial.println("wallfollowsensor");
    wallfollow_sensor();
  }

    else if( digitalRead(r)==LOW)
  {
    //Serial.println("wallfollow_downstair");
    wallfollow_downstair();
  }

  else
  {
//      Serial.println("stopbot");
    stopbot();
  }
//  Serial.println(f_bump);
//  wallfollow();
//  upstair();
//Serial.println("counter1");
//Serial.println(counter1);
//Serial.println("counter3");
//Serial.println(counter3);
  }
  else if(manual_mode==1&&auto_mode==0)
  {
//forward movement code
if(PS3.getButtonClick(UP))
{manual_speed+=10;}
else if(PS3.getButtonClick(DOWN))
{
manual_speed-=10;  
}
if(PS3.getButtonClick(RIGHT))
{lead_speed+=10;}
else if(PS3.getButtonClick(LEFT))
{
lead_speed-=10;  
}
if(PS3.getButtonClick(TRIANGLE))
{
 // assign first lead screw pins to controlled lead screw
 lead1=f;
 lead1_pwm=pwmf;
 lead2=f;
 lead2_pwm=pwmf;
  }
  else if(PS3.getButtonClick(SQUARE))
  {
   //assign middle slider 
   lead1=m;
 lead1_pwm=pwmm;
 lead2=m;
 lead2_pwm=pwmm;
    }
    else if(PS3.getButtonClick(CROSS))
    {
      //assign last lead screw pins
      lead1=b;
 lead1_pwm=pwmb;
 lead2=b;
 lead2_pwm=pwmb;
      }
      else if (PS3.getButtonClick(CIRCLE))
      {
        lead1=f;
 lead1_pwm=pwmf;
 lead2=b;
 lead2_pwm=pwmb;//assign bot lead screw front and backward
        }
 if(PS3.getAnalogHat(LeftHatY) > 137)
{digitalWrite(lead1, LOW);
  analogWrite(lead1_pwm, lead_speed);
  digitalWrite(lead2, LOW);
  analogWrite(lead2_pwm, lead_speed);
  }
  else if(PS3.getAnalogHat(LeftHatY) < 117)
{digitalWrite(lead1, HIGH);
  analogWrite(lead1_pwm,lead_speed);
  digitalWrite(lead2, HIGH);
  analogWrite(lead2_pwm, lead_speed);
  }
  else
  {
    digitalWrite(lead1, HIGH);
  analogWrite(lead1_pwm, 0);
  digitalWrite(lead2, HIGH);
  analogWrite(lead2_pwm, 0);
    }
  
if(PS3.getAnalogHat(RightHatY) > 137)
{digitalWrite(br, LOW);
  analogWrite(pwm3, manual_speed);
  digitalWrite(bl, LOW);
  analogWrite(pwm4, manual_speed);
  digitalWrite(fr, LOW);
  analogWrite(pwm1, manual_speed);
  digitalWrite(fl, LOW);
  analogWrite(pwm2, manual_speed);}
  //backward movement code
else if(PS3.getAnalogHat(RightHatY) < 117)
{
 digitalWrite(br, HIGH);
  analogWrite(pwm3, manual_speed);
  digitalWrite(bl, HIGH);
  analogWrite(pwm4,manual_speed);
  digitalWrite(fr, HIGH);
  analogWrite(pwm1, manual_speed);
  digitalWrite(fl, HIGH);
  analogWrite(pwm2, manual_speed); }
  
  //right Turn code
  else if (PS3.getAnalogButton(R2)>150)
{
 digitalWrite(br, LOW);
  analogWrite(pwm3,manual_speed);
  digitalWrite(bl, HIGH);
  analogWrite(pwm4, manual_speed);
  digitalWrite(fr, LOW);
  analogWrite(pwm1, manual_speed);
  digitalWrite(fl, HIGH);
  analogWrite(pwm2, manual_speed); }
  else if (PS3.getAnalogButton(L2)>150)
{
 digitalWrite(br, HIGH);
  analogWrite(pwm3, manual_speed);
  digitalWrite(bl,LOW);
  analogWrite(pwm4, manual_speed);
  digitalWrite(fr,HIGH);
  analogWrite(pwm1, manual_speed);
  digitalWrite(fl, LOW);
  analogWrite(pwm2,manual_speed); }
  
  else
  {
    digitalWrite(br, HIGH);
  analogWrite(pwm3, 0);
  digitalWrite(bl, HIGH);
  analogWrite(pwm4, 0);
  digitalWrite(fr, HIGH);
  analogWrite(pwm1, 0);
  digitalWrite(fl, HIGH);
  analogWrite(pwm2, 0); }
    
    }

}
void  ps3()
{
  Usb.Task();
}
void ps3_init()
{
#if !defined(__MIPSEL__)
  while (!Serial); // Wait for serial port to connect - used on Leonardo, Teensy and other boards with built-in USb CDC serial connection
#endif
  if (Usb.Init() == -1) {
    Serial.print(F("\r\nOSC did not start"));
    while (1); //halt
  }
  Serial.print(F("\r\nPS3 bluetooth Library Started"));
}

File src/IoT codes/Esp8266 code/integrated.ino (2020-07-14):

//All the dht functions should be used if you are using dth11(temperature sensor) in your project. They are commented in this file.


#include "ESP_MICRO.h" //Include the micro library 
//#include <DHTesp.h> //include this library if  you are using dht11 (temperature sensor)
//DHTesp dht;

//#define DHTpin 14    //D5 of NodeMCU is GPIO14
int testvariable = 0;
const int sensor_pin = A0; 
String S;
void setup(){
  Serial.begin(115200); // Starting serial port for seeing details
  start("ABC","12345678");  // EnAIt will connect to your wifi with given details
  Serial.println();
  Serial.println("Status\tHumidity (%)\tTemperature (C)\t(F)\tHeatIndex (C)\t(F)");
  
  // Autodetect is not working reliable, don't use the following line
  // dht.setup(17);
 
  // use this instead: 
  //**dht.setup(DHTpin, DHTesp::DHT11); //for DHT11 Connect DHT sensor to GPIO 17
  //dht.setup(DHTpin, DHTesp::DHT22); //for DHT22 Connect DHT sensor to GPIO 17
}
void loop(){
  
  //delay(dht.getMinimumSamplingPeriod());
 //float humidity = dht.getHumidity();
 // float temperature = dht.getTemperature();
 
  float moisture_percentage;
  moisture_percentage = ( 100.00 - ( (analogRead(sensor_pin)/1023.00) * 100.00 ) );//taking the reading from the moisture sensor
  S= moisture_percentage;
 
  waitUntilNewReq();  //Waits until a new request from python come
  /* increases index when a new request came*/
  testvariable += 1;
  returnThisStr(S); //returns the reading to the python file, which will in turn render it to the web page.
}

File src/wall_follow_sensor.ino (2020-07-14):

 void wallfollow_sensor() 
 {

    
    if(fldistance>0 && bldistance>0 && number_sensor==0)
    {
        if(fldistance == bldistance )
         {
            angle=0;
         }
        //Serial.println("abcde");
        if( topdistance==0 || topdistance>150 )
        {
          // Serial.println("abcde2");
          straight();
        }
        else if(topdistance<150 && topdistance!=0 && internal_sensor==0)
        {
          stopbot();
          int reading=millis();
          while(millis()-reading<5000)
          {
            digitalWrite(solenoid,LOW);
            digitalWrite(sensor,HIGH);
            analogWrite(pwm_sensor,250);
            
          }
           reading=millis();
          while(millis()-reading<2000)
          {
            digitalWrite(solenoid,LOW);
            digitalWrite(sensor,LOW);
            analogWrite(pwm_sensor,250);
            
          }
          digitalWrite(solenoid,HIGH);
          analogWrite(pwm_sensor,0);
          internal_sensor=1;
        }
        
        else if(topdistance<150 && topdistance!=0 && internal_sensor==1)
        {
          while(angle>-160)
          {
            Serial.println("fghij");
            pingdistance();
            rotateright(-30,-160);
          }
           number_sensor=1;
        }
    }
    
    else if(frdistance>0 && brdistance>0 && number_sensor==1)
    {
        if(frdistance == brdistance )
         {
            angle=0;
         }
        if(topdistance>75 ||topdistance==0)
        {
          straight();
        }
          number_sensor=2;
        }
    



    else if(number_sensor==2)
    {
      stopbot();
      main_state=5;
    }
 }

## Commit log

2020-07-12 Update and rename Arduino_codes/final_bot.ino to src/final_bot.ino
2020-07-12 Image of Soil Sensor used
2020-07-13 Create 38 CM steel channel.SLDPRT
    [38 CM steel channel.SLDPRT]
2020-07-13 Create 59CM steel channel.SLDPRT
    [59CM steel channel.SLDPRT]
2020-07-13 Create Al channel LeadScrew support.SLDPRT
    [Al channel LeadScrew support.SLDPRT]
2020-07-13 Create base plough.SLDPRT
    [base plough.SLDPRT]
2020-07-13 Create Bearing Block Johnson's motor.SLDPRT
    [Bearing Block Johnson's motor.SLDPRT]
2020-07-13 Create channel seeder.SLDPRT
    [channel seeder.SLDPRT]
2020-07-13 Create DC LeadScrew 900Rpm.SLDPRT
    [DC LeadScrew 900Rpm.SLDPRT]
2020-07-13 Create DC motor Clamp UP.SLDPRT
    [DC motor Clamp UP.SLDPRT]
2020-07-13 Create DC Motor.SLDPRT
    [DC Motor.SLDPRT]
2020-07-13 Create encoder gear left helical.SLDPRT
    [encoder gear left helical.SLDPRT]
2020-07-13 Create FRONTAL BLADE SET plough.SLDPRT
    [FRONTAL BLADE SET plough.SLDPRT]
2020-07-13 Create johnsons motor mount.SLDPRT
    [johnsons motor mount.SLDPRT]
2020-07-13 Create Idler Wheel Channel Mount.SLDPRT
    [Idler Wheel Channel Mount.SLDPRT]
2020-07-13 Create lead mount Support channel vertical.SLDPRT
    [lead mount Support channel vertical.SLDPRT]
2020-07-13 Create lead screw 8mm.SLDPRT
    [lead screw 8mm.SLDPRT]
2020-07-13 Create Lead Support Connecting channel.SLDPRT
    [Lead Support Connecting channel.SLDPRT]
2020-07-13 Create Lead support Laid channel up.SLDPRT
    [Lead support Laid channel up.SLDPRT]
2020-07-13 Create LeadScrew thread.SLDPRT
    [LeadScrew thread.SLDPRT]
2020-07-13 Create Linear Bearing, 8mm Shaft.SLDPRT
    [Linear Bearing, 8mm Shaft.SLDPRT]
2020-07-13 Create Plough assembly.SLDASM
    [Plough assembly.SLDASM]
2020-07-13 Create SEED container.SLDPRT
    [SEED container.SLDPRT]
2020-07-13 Create seeder assembly.SLDASM
    [seeder assembly.SLDASM]
2020-07-13 Create slider channel side.SLDPRT
    [slider channel side.SLDPRT]
2020-07-13 Create solenoid valve.SLDPRT
    [solenoid valve.SLDPRT]
2020-07-13 Create steel channel 60cm.SLDPRT
    [steel channel 60cm.SLDPRT]
2020-07-13 Create WHEEL bearing block.SLDPRT
    [WHEEL bearing block.SLDPRT]
2020-07-13 Create wheel coupling 2.SLDPRT
    [wheel coupling 2.SLDPRT]
2020-07-13 Create wheel coupling.SLDPRT
    [wheel coupling.SLDPRT]
2020-07-13 Create Wheel idler.SLDPRT
    [Wheel idler.SLDPRT]
2020-07-13 Create WHEEL Plate 3mm Bearing.SLDPRT
    [WHEEL Plate 3mm Bearing.SLDPRT]
2020-07-13 Create WHEEL Plate 3mm.SLDPRT
    [WHEEL Plate 3mm.SLDPRT]
2020-07-13 Create ball bearing Block 8mm.SLDPRT
    [ball bearing Block 8mm.SLDPRT]
2020-07-13 Create DC motor Clamp BOTTOM.SLDPRT
    [DC motor Clamp BOTTOM.SLDPRT]
2020-07-13 Create DC support Channel.SLDPRT
    [DC support Channel.SLDPRT]
2020-07-13 Create Bearing block Lead Screw up.SLDPRT
    [Bearing block Lead Screw up.SLDPRT]
2020-07-13 Create helical GEAR assem.SLDASM
    [helical GEAR assem.SLDASM]
2020-07-13 Create Idler Wheel Castor.SLDPRT
    [Idler Wheel Castor.SLDPRT]
2020-07-13 Differential Chassis Images Upload
2020-07-13 Sample Micro-controller Image
2020-07-13 CAD Images Update
    [38 CM steel channel.SLDPRT, 59CM steel channel.SLDPRT, 8mm Ball Bearing.SLDPRT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]
